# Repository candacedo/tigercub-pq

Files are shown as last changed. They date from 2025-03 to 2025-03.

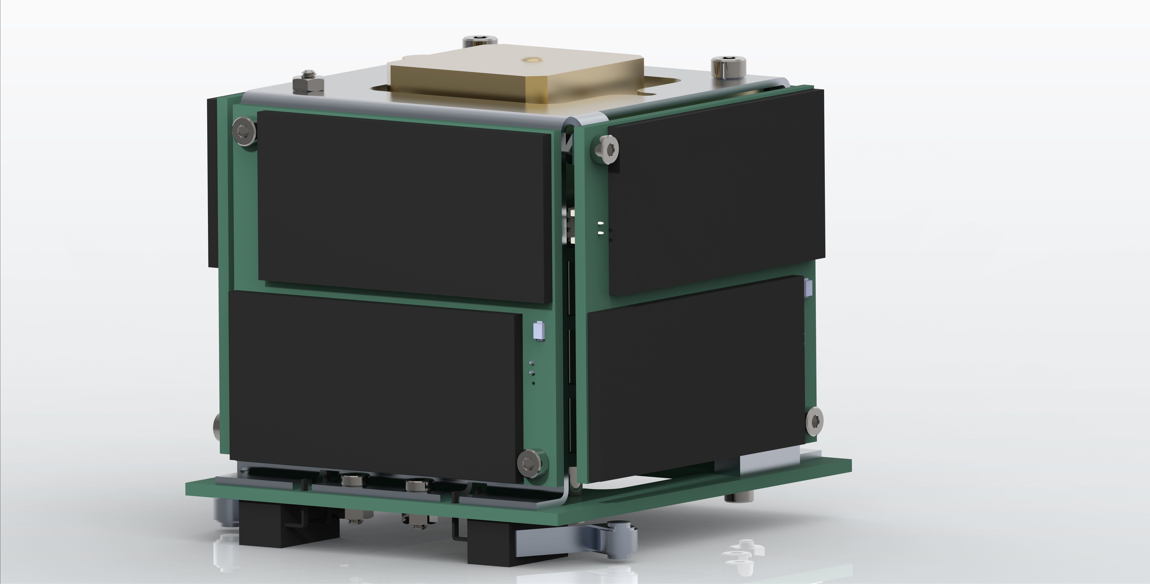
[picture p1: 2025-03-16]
CAD/full-assembly-the-beast.jpg

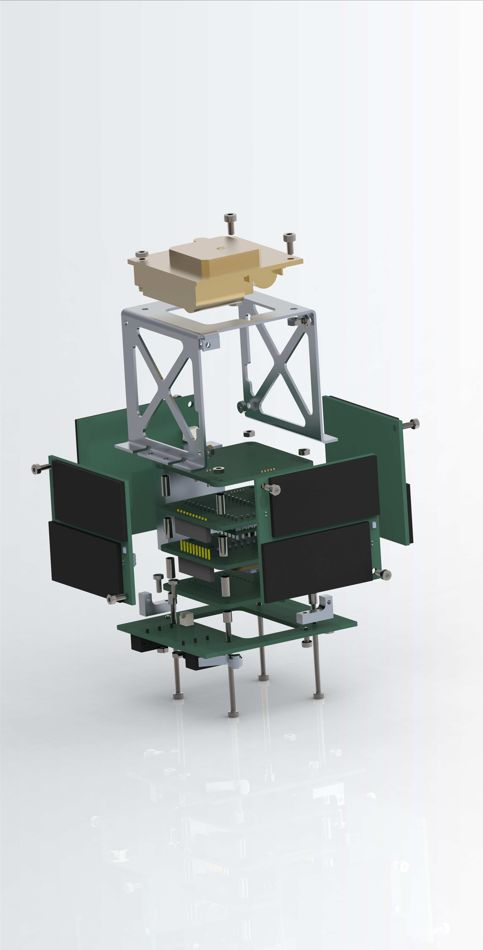
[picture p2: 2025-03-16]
CAD/full-assembly-exploded.jpg

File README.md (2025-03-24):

# TigerCub PocketQube Platform
TigerCub, an accessible, mission-agnostic PocketQube platform.

TigerCub is a satellite bus in the PocketQube form factor, designed to be accessible to students and amateur nanosatellite developers. It uses primarily commercial-off-the-shelf (COTS) components and relatively simple custom-designed PCBs, lowering barriers of entry for developers who are venturing into the PocketQube world. 

I developed TigerCub for my undergraduate senior independent work. The vast majority of design work is complete and some subsystems have been tested in laboratory environments, but the satellite bus has yet to undergo full functional testing and testing in flight-like environments. Please use at your own risk.     

## Technical Overview
TigerCub includes the following subsystems:
* on-board computer and attitude determination system,
* electrical power system,
* radio communication system, and 
* chassis.

The on-board computer/attitude determination system features an Arduino-programmable Teensy 4.0 as well as a COTS IMU and COTS MicroSD storage from SparkFun. The communication system uses the RockBLOCK 9603, a compact and lightweight communications module that transmits and receives via the Iridium network. The electrical power system is composed of a power management and distribution module designed by BHDynamics, custom-designed solar panels, and a Lithium-ion battery. These subsystems are all integrated into a sheet-metal chassis, with additional space for a payload. 

All CAD was created in PTC Creo Parametric (Version 9.0.0.0), which is free for students. All schematics and PCB designs were created in KiCAD, a free EDA software. 

## Documentation
For additional technical and operational details, including design decisions, bill of materials, power and thermal analyses, and sample code, see the "TigerCub_Report" PDF file in the repository. Please reach out to cdo32 \[at\] gatech \[dot\] edu or mgalvin \[at\] princeton \[dot\] edu for further questions. 

## Future Work & Things to Fix
A few features that should to be fixed/added (not an exhaustive list):
* Kill switches should serve as a break point between the battery and the on-board computer instead of just being connected to the on-board computer. This will involve some redesign of the backplate and wire routing. 
* Flight software needs to be developed for the EPS module and expanded upon for the flight computer. (See technical report for additional details.)
* The RockBLOCK radio system has two electrolyic supercapacitors that are a potential outgassing risk. These should be swapped out for space-qualified capacitors.
* The thermal analysis (see technical report) suggests that the spacecraft may operate outside the temperature limits of the battery. The battery should be insulated to protect it from temperature extremes. See technical report for a few suggestions.

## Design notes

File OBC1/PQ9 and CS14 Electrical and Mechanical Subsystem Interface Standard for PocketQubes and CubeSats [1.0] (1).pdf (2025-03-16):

### PQ9 & CS14 Interface Definition

Document:
Issue:
Page:

DPQ-TUD-IC-02

CC-BY-ND
This document is written and maintained by Delft University of Technology. It can be freely distributed and (parts) may be copied for own purposes with appropriate attribution and without changing the context of the information stated.

# PQ9 & CS14 Electrical and Mechanical Subsystem Interface Standard for PocketQubes and CubeSats

Description: This document defines the use and implementation PQ9 and CS14 standard.

Revision Record

Issue | Date | Author / Editor | Reviewer | Affected Sections | Description
0.1 | 15-5-17 | J. Bouwmeester | | All | Document initiation
0.2 | 22-5-17 | J. Bouwmeester | | 0 | Electrical characteristics added
0.3 | 22-5-17 | J. Chia | | Appendix A | Compatibility appendix added
0.4 | 29-5-17 | M. Boerci | | 0, 4.7, 0 | Added mechanical characteristics, reset line description and pin definition
0.5 | 17-10-17 | S. Radu | | 1,3,4 | Added scope and introduction; Changed mechanical characteristics – added spacers explanation.
0.5 | 18-10-17 | S. Radu | | 5, appendix B | Added reference data bus architecture Added appendix with drivers
0.6 | 22-11-2017 | J. Bouwmeester | | all | Rewritten towards public standard
0.7 | 23-05-2018 | J. Bouwmeester | | 5 | Modifications on data link protocol
1.0 | 04-07-2017 | J. Bouwmeester | | 4,5 | Added missing parts on grounding, termination and updated data link protocol. Document made ready for first public release.

CC-BY-ND

## Table of Contents

CC-BY-ND

## 1 Background

At Delft University of Technology (TU Delft), long term research in CubeSat electrical interface standards revealed many issues with the versatile adaptation of the PC/104 electrical interface standard. The main issuesidentified are the major amount of bus lockups on the I²C data bus interface, the volume consumption of the relatively big 104 pin connector and the potential compatibility issues arising from different manufacturers assigning different functions to unused/general purpose pins[1]. Also for power distribution the existing standards provide limited clarity and power efficiency [2]. Similar to the PC/104 implementation on CubeSats, a versatile electrical and mechanical interfaces standard under the name PQ60 already exists [3].

The versatility of the PC/104 and PQ60 standards, having multiple data busses to choose from and the freedom to allocate custom signals or power to general purpose pins, are appreciated by many engineers. Since both standards are implemented already in commercial products at the time of initiation of this document, they are a logical option to consider as main bus standard. However, the definition of a lean and unambiguous alternative standard for PocketQubes and CubeSats was deemed necessary in attempt to overcome identified issues and be prepared for the future.

The aim in selecting the interface standard for the satellites developed at TU Delft was to have lean, small, efficient and resilient interface. For selecting the data bus, I²C, Differential I²C, CAN and RS-485 were taking into consideration and the main criteria were robustness, power consumption, effective data throughput and legacy support were taken into account. The details of the trade-off can be found in a journal paper [4]. The PocketQube and CubeSat community has been involved in the research and the trade-off process for the data bus with the aid of surveys. However, the detailed definition of the PQ9 and CS14 standards are performed at TU Delft to aid a rapid definition process and avoid compromising its lean philosophy.

## 2 Use of the Standard

The standard is open, non-proprietary and free to use for commercial and non-commercial entities. The PQ9 and CS14 standards are not trademarked. However, the logos may only be used for systems which are fully compliant to the respective standards. New (derived) standards should use a different logo and naming in order to avoid confusion and to maintain the lean philosophy and unambiguous implementation of PQ9 and CS14.

Delft University of Technology will remain the responsible entity for the maintenance of this document. In the near future, potential updates will focus on the clarity, correctness and completeness of the document. Comments from the community related to the documents and the specified details are welcome. Changes to the standard on the high level are undesired and will not occur if no major flaws will be discovered during the verification process which is expected early 2018. Future improvements of the standard will only be performed when the interface becomes a limiting factor for the state-of-the-art technology. This is not expected in upcoming years and when this is deemed necessary the aim will be to provide backwards compatibility with the existing standard.

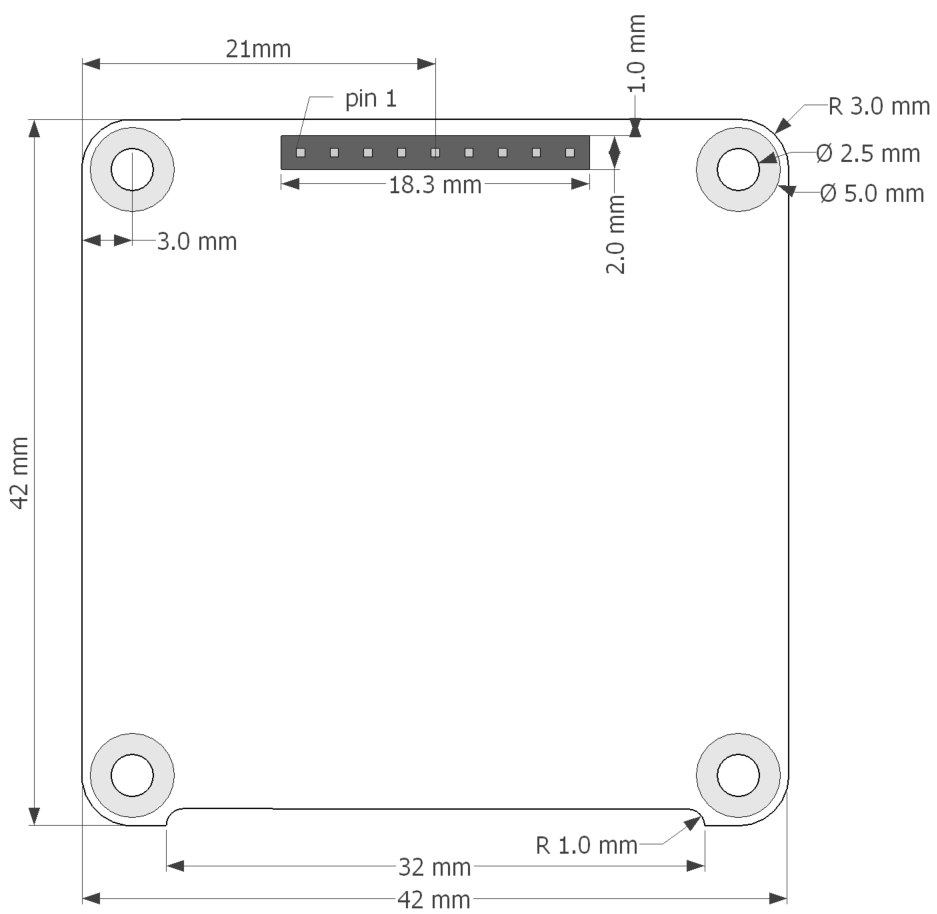
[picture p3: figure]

CC-BY-ND

## 3 Mechanical Characteristics

Each physical subsystem will be placed in a stack and has standard outer (PCB) dimensions and four holes for mechanical fixation to the rest of the systems and/or satellite body. The mechanical outline of the boards are compatible to the CubeSat Design Specification [5] and the PocketQube Standard [6].

### 3.1 In-Plane System Envelope

The standard Printed Circuit Board (PCB) outline of PQ9 and CS14 is provided in Figure 1 and Figure 2 respectively. The room between the edges of the PCB and the outer structure of the satellite can be used by cabling and extensions toward the outside of the satellite. It is recommended to limit in-plane extensions of components and use of flexible wiring which can be rerouted when necessary.

Figure 1. PQ9 printed circuit board outline

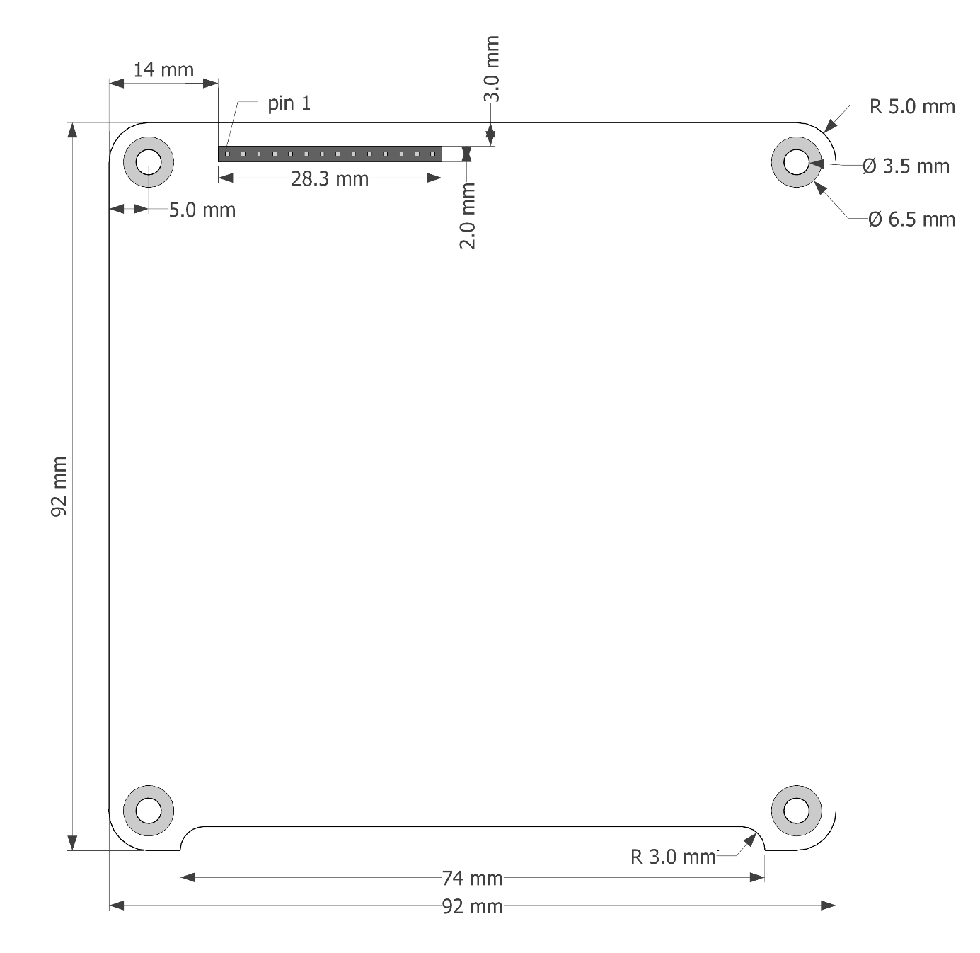
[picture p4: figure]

CC-BY-ND

Figure 2. CS14 printed circuit board outline

### 3.2 Out-of-Plane System Envelope

The out of plane dimensional constraint depends on the selection of the connector(s) and possible configurations. The following requirements have to be taken into account:

- Each system has a minimum (out-of-plane) component height of 2 mm on the bottom side of the PCB. This minimum value is used for a system with only leads on the bottom of a small connector. Note that the connector of the system below protrudes into the system envelope under consideration.
- A 1 mm margin is required between components on the top side of the PCB and possible components on the bottom side of the next PCB.
- The PCB thickness is assumed to be 1.6mm. In case of other PCB thickness, the potential configuration(s) need to be recalculated. Please pay attention to the minimum and maximum pin insertion depth.

CC-BY-ND

- The maximum pin soldering height is 0.65 mm.
- The rods or threaded stand-offs thread diameter is M2 for PocketQubes and M3 for CubeSats.
- The outer diameter of the spacers or stand-offs is 5 mm for PocketQubes and 7 mm for CubeSats.

The reference connector is the Samtec SQT-1xx-xx-LS series, which provides the input stated below.

- The connector height is equal to 6.35 mm [RD01]
- The pin (lead) length of the small connector (SQT-109-03-LS for PocketQubes, SQT-114-03-LS for CubeSats) is equal to 5.28 mm [RD01]
- The pin (lead) length of the large connector (SQT-109-02-LS for PocketQubes, SQT-114-02-LS for CubeSats) is equal to 15.24 mm [RD01]
- The insertion depth is required to be between 2.62 and 5.03 mm [RD01], whereas for PQ9 and CS14 the minimum and maximum considered insertion depths are respectively 3 and 5 mm.
- Connectors if different vendors may be considered is they are fully compatible with the reference connector. In case the potential pin (lead) lengths are different, the potential configurations need to be recalculated.

CC-BY-ND

Figure 3 and Table 1 provides an example based on two systems using the small connector and a board to board distance (spacer) of 7 mm in between.

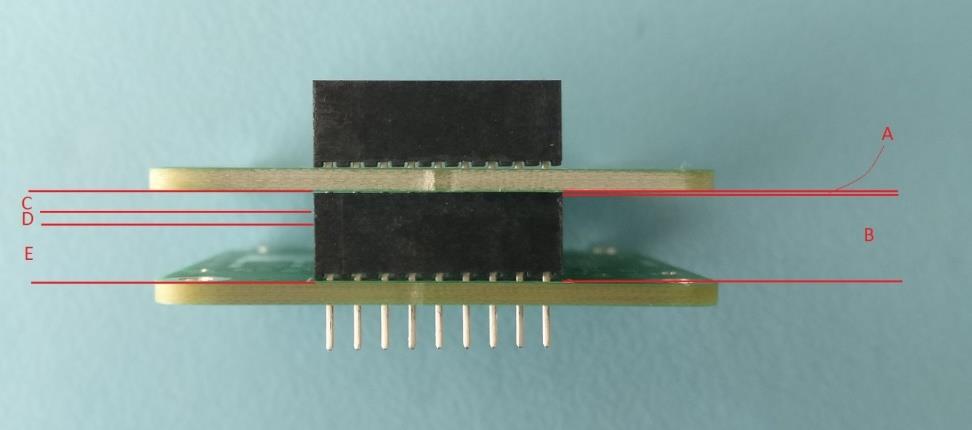
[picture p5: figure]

Figure 3: Out-of-plane constraints example (option I)

Table 1: Values of maximum component height and insertion depth (option I)

Symbol | Description | Value [mm]
A | Maximum soldering pad height | 0.65
B | Connector height | 6.35
C | Maximum height of components placed underneath upper PCB | 2.00
D | Margin between components of two adjacent PCBs | 1.00
E | Maximum component height | 4.00
tPCB | PCB thickness | 1.60
Lpins,small | Pin length of the small connector | 5.28
Idepth | Pin Insertion Depth | 3.03

CC-BY-ND

Table 2 provides the values for different configurations of the small and large reference connector. When using these values, please check if they comply with the assumptions made.

Table 2: Configuration possibilities with small and large connectors

Description | Max. comp. height above PCB [mm] | Max. comp. height below PCB [mm] | Board spacing dist.¹ [mm] | Pin insert depth [mm] | Stack height inc. 1mm margin [mm] | Example Image

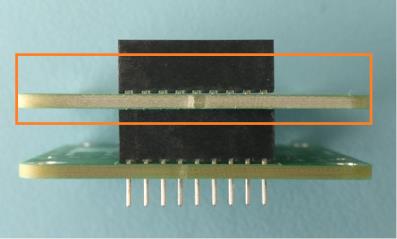
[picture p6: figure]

Option I: single small connector on top | 4.0 | 2.0 | 7.0 | 3.0 | 8.6 mm

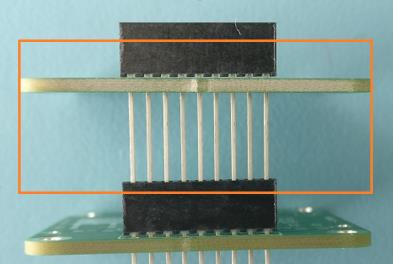
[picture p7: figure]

Option II: single large connector on top | 4.0 4.0 4.0 | 10.0 11.0 12.0 | 15.0 16.0 17.0 | 5.0 4.0 3.0 | 16.6 17.6 18.6

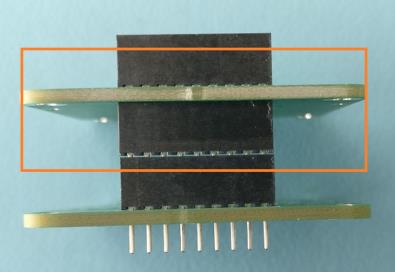
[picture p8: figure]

Option III: small connector on top, small connector glued on bottom² | 4.0 | 9.0 | 14.0 | 3.9 - 4.6 | 15.6
Option IV: double small connector stacked on top³ | 11.0 | 2.0 | 14.0 | 3.0 | 15.6

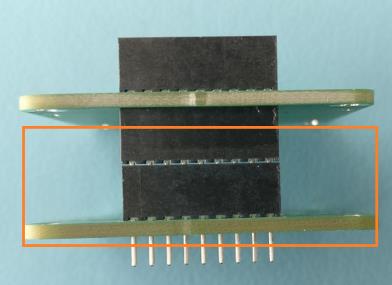
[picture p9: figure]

1) This board spacing distance stated is the distance from the PCB surface of the largest side to the next system’s PCB surface, assuming that the next system uses only a single small connector. In case the next system uses a different configuration, spacing distance needs to be calculated for this configuration.
2) fixation of bottom connector (e.g. with glue) at a spacing distance between 0.0 and 0.65 mm from the PCB is essential to prevent that this connector can slide downwards and the connector on top goes below minimum insertion depth.
3) Fixation of stacked connector at exactly 0.65mm spacing (e.g. with glue) is required to prevent that the insertion depth of the PCB above goes below minimum insertion depth.

CC-BY-ND

table continued

Description | Max. comp. height above PCB [mm] | Max. comp. height below PCB [mm] | Board spacing dist.¹ [mm] | Pin insert depth [mm] | Total stack height inc. 1mm margin [mm] | Example Image

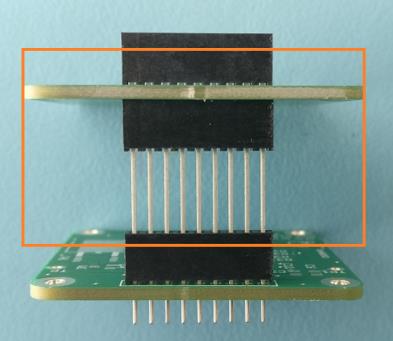
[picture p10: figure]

Option V: small connector on top, large connector on bottom | 4.0 | 19.0 | 24.0 | 3.9 - 4.6 | 25.6

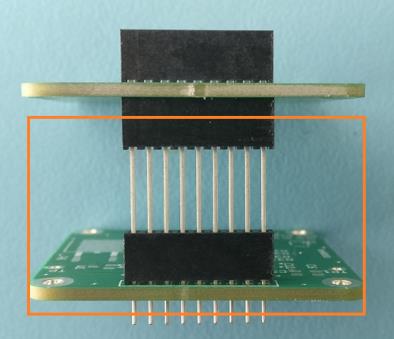
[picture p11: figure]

Option VI: small connector on top, large connector stacked on top of small connector | 21.0 | 2.0 | 24.0 | 3.9 -3.6 | 25.6
Option VII: large connector on top, large connector on bottom | 4.0 4.0 | 27.0 28.0 | 32.0 33.0 | 4.6 – 5.0 3.6 – 5.0 | 33.6 34.6

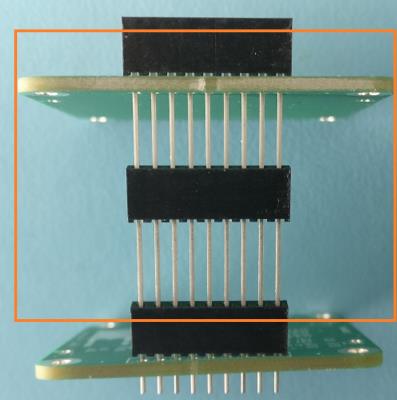
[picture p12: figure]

1) This board spacing distance stated is the distance from the PCB surface of the largest side to the next system’s PCB surface, assuming that the next system uses only a single small connector. In case the next system uses a larger sizing as well, spacing distance needs to be calculated for this configuration.

CC-BY-ND

## 4 Electrical Characteristics

### 4.1 Pin Definition

Both PQ9 and CS14 are based on a single linear RS-485 data bus, several unregulated power distribution lines, a few (common) ground lines and a reset line.

The PQ-9 and CS14 interface connector pin allocations are represented in Figure 4 and Figure 5 respectively and their definition is stated in Table 3.

Figure 4. PQ9 (pin 1-9) interface connector

Figure 5. CS14 interface connector

Table 3. Pin allocation for PQ9/CS14 standard interface

Pin | Signal | Allocation
1 | RST | system reset line (60 Ω to gnd)
2 | 485-B | RS-485 inverting signal
3 | 485-A | RS-485 non-inverting signal
4 | GND | Ground
5 | V1 | rec.: OBC (PQ: + Radio)
6 | V2 | rec.: ADCS (PQ: + GNC)
7 | V3 | rec.: propulsion
8 | V4 | rec.: primary payload(s)
9 | GND | Ground
10 | V5 | rec.: radio
11 | V6 | rec.: GNC
12 | V7 | rec.: data storage & payload
| | data transmitter
13 | V8 | rec.: secondary payload(s)
14 | GND | ground

### 4.2 RS-485 Clock Frequency

The internal microcontroller’s UART will be set at a baud rate of:

500 kbit/s (500,000 bit/s) for PQ9

and

1 Mbit/s (1,000,000 bit/s) for CS14.

The clock at any subsystem may not be off by more than +/- 0.5% to ensure reliable communications. It is recommended to select the general clock frequency of the microcontroller at least 16 times higher than the baud rate (this yields 8 MHz for PQ9 and 16 MHz for CS14) .

1

RST

2

485A

3

485B

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
485A

3

485B

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
CC-BY-ND

### 4.3 RS-485 Compatible Microcontrollers

The microcontroller should have a UART which supports the stated clock frequency. The UART should also support 9 bits between start and stop conditions (see byte definition in section 5.1). However, it is recommend that a hardware controlled address bit detection which triggers and interrupt is included to limit the amount of data (interrupts) which need to be processed by the microcontroller. Developers using the standard should always check if a chosen microcontroller supports the byte and packet definition. Appendix A shows the compliance of a selection of microcontrollers with these requirements.

### 4.4 RS-485 Differential Drivers

There is a wide variety of differential drivers which can be chosen. In the current version of the standard no specific recommendations are given. An important criteria is the supported baud rates. For PQ9 this should be at least 500 kbit/s, for CS14 it should be 1 Mbit/s. Furthermore, the size of the integrated circuit and its power consumption could be important criteria to consider for which significant differences between options can be expected. Finally, slew rate limited devices are more immune to noise but it comes at the expense of a restricted supported data rate.

### 4.5 RS-485 Termination and Biasing

Reflection is not really a concern up to 1 MHz for PocketQubes and CubeSats, since the wavelength (~300m) in this case is orders of magnitude longer than the line length. There is thus no need to put the termination at the end of the lines to suppress reflection. For increased noise immunity however, single termination at an arbitrary point along the line is highly recommended. The chosen location for the standard is the physical board which acts as the central unit for the electrical power distribution. The reason is that such a system is always required for the CS14 and PQ9 interface standard to distribute power. A central on-board computer, being a likely master node for RS-485, is more likely to be redundant or could be integrated with another physical subsystem, yielding potential missing or redundant termination resistors in the system. The termination resistance should be 60 Ω or more. The higher the resistance, the lower the power consumption but this also reduced noise immunity.

Old generation differential drivers specify bias resistors to enforce a logic high during idle state by pulling line A to the reference voltage and line B to ground. The bias resistors can only be implemented if there is also a termination resistor and it is recommended to have a bias resistor value of 5 to 10 times the termination resistance. This forces the operation out of the undefined region between +/-200 mV. New generation RS-485 drivers, such as the LTC1480, MAX3471 and TI SN64HVD7x have an internal fail-safe feature which do not require external biasing anymore. However, for enhanced noise immunity it can still be implemented.

### 4.6 Power Distribution Voltage Level and Current Limits

The distribution voltage levels are:

PQ9: 3.0 V – 4.1 V
CS14: 6.0 V – 8.2 V

CC-BY-ND

These levels are based on a single Li-Ion battery cells and two in series respectively. By distributing unregulated battery voltage levels and leaving potentially required regulation to fixed voltage levels to the local subsystems, complexity is avoided and conversion efficiency losses are minimized [3].

The absolute maximum current is 4 A per distribution line, as determined by the connector specification assuming a maximum internal temperature of 60 °C [6]. The allowed current levels can however be lower due to the battery limitations and the power budget. It is recommended to include programmable current limiters for each distribution line.

In-rush current limits are not yet specified in this standard. Therefore, the specifications of the chosen central electrical power distribution unit needs to be followed. It is generally recommended to limit the in-rush current as much as possible at the subsystem loads.

### 4.7 Grounding Topology

The ground pins on the PQ9 and CS14 function as common reference ground as well as power return path. This could lead to small voltage difference across a stack of physical subsystems due to their power consumption. According to [2], an extreme case of stack of 10 boards over 20 cm distance w.r.t. the electrical power distribution unit, would yield 44 mΩ resistance for one grounding path. Assuming that this should carry a return current of 4A, a maximum ground voltage offset of 200 mV can be expected. To minimize ground loops, it is important that electrically conducting structural components (for example metallic stand-offs or spacers at the corners) are only connected to the ground via a resistor of at least 1 kΩ to ensure that the electrical interface ground carries the current and not the structural elements. All electronic circuits must be connected to the PQ9/CS14 ground with a minimal path resistance.

### 4.8 Reset Line

A global power reset will be triggered when the line is pulled high for at least 20 ms to a minimum threshold voltage of 2 V and at maximum 5 V. At both sides of the reset line, this period should be ensured with margins appropriate for the circuit and its (thermal) environment. The driving circuit can be placed e.g. at the radio command receiver (for a tele-commanded reset) or at the on-board computer (for automatic failure detection, isolation and recovery purposes).

After a reset has been triggered, the central EPS unit is required to switch off the distribution power to all subsystems and its own microcontroller for 2000 ms. All subsystems should ensure that local power has dropped to a level which guarantees a complete power-out of volatile memory and register states within 2000 ms taking appropriate margins into account.

CC-BY-ND

A standard filter and protection circuit shall be implemented close to the power reset (integrated) circuit:

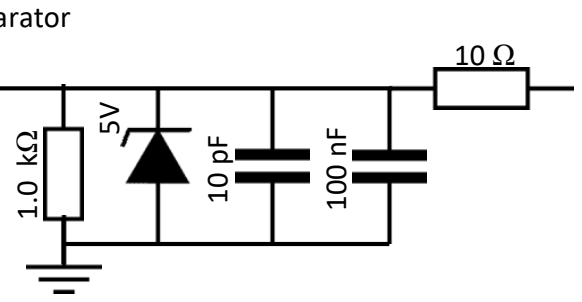
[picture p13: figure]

The shunt bias resistor pulls the line low in idle conditions. A minimum direct current of 2 mA is required to pull the line to the threshold voltage.

The input series resistors in combination with the Zener diode protects the circuit for excessive voltage levels due to electrostatic discharge and particle radiation.

The RC filter caps have a cut-off frequency of 1.6 kHz and 16 MHz to filter out power transient and RF noise respectively.

PQ9 connector

comparator
input

CC-BY-ND

## 5 Data Link Protocol

The data protocol used for PQ9 is currently only defined at the data link layer.

### 5.1 Byte Definition

- The chronological order is Least Significant data Bit (LSB) first
- Each byte begins and ends with a start and stop bit (UART standard)
- The address interrupt bit follows after the Most Significant data Bit (MSB). When this bit is 1, the byte contains an destination address. For any other type of byte it is 0.

This figure relates to the chronological order and not the logical order where bit 7 is on the left.. Please note that for human interpretation the 8 content bits need to be reversed in order (bit 7 on the left).

### 5.2 Packet Definition

- Destination/Source Address:
- Defines the source and destination of the packet.
- Supports up to 254 nodes (inc. master).
- Master address: 0x00.
- General call address: 0xFF.
- Slave address: anything between 0x01 and 0xFE.
- Message Size:
- Defines the length of the message in bytes.
- Size=0x00 is used for acknowledgements.
- Supports messages up to 255 bytes.
- Refers only to the message content, so total packet size is message size + 5 bytes.
- CRC:
- CRC-16 CCIT
- Initialized on seed: 0xFFFF
- Calculated on complete packet (so address, size + message data)
- Calculated on least significant bit first
start | 0 | 1 | 2 | 3 | 4 | 5 | 6 | 7 | address | stop

destination
adress
[8 bit]

message
size
[8 bit]

source
address
[8 bit]

message
[0-255 bytes]

CRC
[16 bit]

CC-BY-ND

### 5.3 Data Transactions

There is only a single master node active at a time. All other devices are slave nodes and only respond upon request of the master. A redundant/back-up node which is slave or off in nominal conditions can take over the master functionality provided that the nominal master is not active on the bus anymore.

There are three types of transactions:

### 1. Individual message

master → slave

slave → master

### 2. Data request

master → slave

slave → master

### 3. General call

master → slave

slaves do not respond (this should be enforced at each slave when called on the general address)

slave
address

message
size

master
0x00

one-way command/data

CRC
[16 bit]

master
0x00

ack.
0x00

slave
address

CRC
[16 bit]

slave
address

message
size

master
0x00

data request command

CRC
[16 bit]

master
0x00

ack.
0x00

slave
address | response data

CRC
[16 bit]

all
0xFF

message
size

master
0x00

one-way command/data

CRC
[16 bit]

CC-BY-ND

### 5.4 Error Handling

CRC Failure

When the CRC failed, the data packet should be discarded as a whole by the microcontroller. This minimizes the chance that slaves respond on a message which was not meant for them (e.g. bitflip on destination address) or master or slave start to interpret noise.

Time-out

The maximum time-out is 100 ms, including latency and time intervals between bytes. The counter starts at the master after the destination address byte is sent and by the slave when the it identifies its own address (or the general address). When the entire transaction is not completed within this time, both slave and master discard the information which is send. The master will internally flag that the transaction is timed-out, such that it could potentially be used by the application layer for error handling.

## 6 References

1. Bouwmeester J. et al., Survey on the implementation and reliability of CubeSat electrical bus interfaces, CEAS Space Journal Vol 9, . doi: 10.1007/s12567-016-0138-0, 2017.
2. Bouwmeester J. and Santos N., Analysis of the Distribution of the Electrical Power in CubeSats, The 4S symposium. ESA, Valetta, 2014.
3. Becnel E. et al., PQ 60 Standard Document (v1.1), 2015.
4. Bouwmeester J. et al., Towards an innovative electrical interface standard for PocketQubes and CubeSats,. Adv Sp Res. doi: 10.1016/j.asr.2018.03.040, 2018.
5. California Polytechnic State University., Cubesat design specification, 2009.
6. Radu S. et al., The PocketQube Standard, 2018.

CC-BY-ND

## Appendix A Microcontroller-Byte Definition Compatibility

A sample selection is made of 8 microcontrollers (to be) used in PocketQubes and CubeSats, to check if the UART controller supports the byte definition, with emphasis on the address bit as interrupt. The results are provided in the following table:

Manufacturer | Microcontroller | Satellite | Can an address bit (9-bit UART) be implemented on the micro-controller? | Does the address bit trigger a dedicated interrupt? | Note
Texas Instruments | MSP432 | Delfi-PQ | Y | Y | MSP432 Technical Reference manual, pg 725-753 Keyword: Address-Bit Multiprocessor Format, pg 729
Texas Instruments | MSP430 | Alba Orbital OBC | Y | Y | MSP430 User's Guide, pg 571- 599 Keyword: Address-Bit Multiprocessor Format, pg 575
Atmel | AT91SAM9G20 | ISISpace CubeSat OBC | Y | Y | Atmel SAM9G20 datasheet pg 354-376, 481-535 Keyword: Multidrop mode, PARE, pg 500
ARM | Cortex-M3 STM32F103C8T6 | AAUSAT-3, OzQube camera module | ? | Y | RM0008 Reference manual, pg 790-832 Keyword: Address mark detection, WAKE, RXNE flag, pg 806 Address bit at MSB, used 4-bit address format, the 4-bit address is at LSB
Atmel | AT32UC3C | GOMSpace CubeSat OBC | Y | Y | Atmel AT32UC3C datasheet pg 562-656 Keyword: Multidrop mode, PARE, pg 584
Atmel | ATmega328P | Arduino, OzQube, ArduiQube | Y | Y | Atmel ATmega328/P datasheet pg 225-253 Keyword: Multi-Processor Communication Mode, pg 239
ARM | Cortex-M4 MK20DX256 | Ubo PocketQube, Smog-1 | Y | Y | K20 Sub-Family Reference Manual pg 1201-1296 Keyword: Match address operation, pg 1274
MicroChip | PIC32MM0064FP L028 | Low power, latest generation | Y | Y | PIC32MX Family Reference Manual pg 699-752 Keyword: Address Detect Mode, pg732

### PQ9 & CS14 Interface Definition

Issue:
Page:

1.0
18 / 19

CC-BY-ND
This document is written and maintained by Delft University of Technology. It can be freely

## Appendix B Potential RS485 drivers

The list below provide a list of potential RS-485 drivers which can be used with their key specifications. Note that this list is not complete and will not be kept up to date. It focusses on the data rates required for PQ9 and CS14 and is limited to solder mounted devices.

No | | | Max. Data rate (Mbit /s) | Curr ent (idle, Rx on) [mA] | Power (driving, 120Ω termin ation) [mA] | Packa ge | width (mm) | lengt h (mm) | Voltage range | Temp. Range (deg C) | Featu res | Datasheet
1. | Intersil | ISL32455 EIUZ | 1 | 2.1 | 54 or 100 | 8-MSO P | 3.05 | 5.05 | 3 | 5.5 | -40 | 85 | +-60V Fault | https://www.intersil.com/content/dam/Intersil/documents/isl3/isl32450e-52e-53e-55e-57e.pdf
2. | Intersil | ISL32455 EIBZ | 1 | 2.1 | 54 or 100 | 8-SOIC | 3.05 | 5.05 | 3 | 5.5 | -40 | 85 | +-60V Fault | https://www.intersil.com/content/dam/Intersil/documents/isl3/isl32450e-52e-53e-55e-57e.pdf
3. | Intersil | ISL32435 EIUZ | 1 | 2.1 | 54 or 100 | 8-MSO P | 3.05 | 5.05 | 3 | 5.5 | -40 | 85 | +-40V Fault | https://www.intersil.com/content/dam/Intersil/documents/isl3/isl32450e-52e-53e-55e-57e.pdf
4. | Intersil | ISL32435 EIBZ | 1 | 2.1 | 54 or 100 | 8-SOIC | 3.05 | 5.05 | 3 | 5.5 | -40 | 85 | +-40V Fault | https://www.intersil.com/content/dam/Intersil/documents/isl3/isl32430e-32e-33e-35e-37e.pdf
5. Exar | Corporati on | XR33155 | 1 | 4 | 120 | 8-SOIC | 3.05 | 5.05 | 3 | 5.5 | -40 | 85 | +-60V Fault | https://www.intersil.com/content/dam/Intersil/documents/isl3/isl32430e-32e-33e-35e-37e.pdf
6. Exar | Corporati on | XR33038 | 1 | 0.3 | 120 | 8-NSOI C | 6 | 5 | 2. 8 | 5.5 | -40 | 85 | +-18V Fault, receiv er input filteri ng | https://www.exar.com/ds/xr33152-xr33155-xr33156-xr33158.pdf

### PQ9 & CS14 Interface Definition

Issue:
Page:

1.0
19 / 19

CC-BY-ND
This document is written and maintained by Delft University of Technology. It can be freely
7. Exar | Corporati on | XR33035 | 10 | 0.3 | 120 | 8-NSOI C | 6 | 5 | 2. 8 | 5.5 | -40 | 85 | +-18V Fault, receiv er input filteri ng | https://www.exar.com/ds/xr33032-35-38_v100_022814.pdf
8. Maxim | Integrate d | MAX147 82EAUA | 1 | 1.9 | 54 or 100 | 8-SO | 5 | 6.2 | 3 | 5.5 | -40 | 85 | | https://www.exar.com/ds/xr33032-35-38_v100_022814.pdf
9. Maxim | Integrate d | MAX147 82EATA | 0.5 | 1.9 | 54 or 100 | 8-TDFN -EP | 3.1 | 3.1 | 3 | 5.5 | -40 | 12 5 | | http://datasheets.maximintegrated.com/en/ds/M AX14782E.pdf
10. Maxim | Integrate d | MAX147 82EASA | 0.5 | 1.9 | 54 or 100 | 8-uMA X | 3.1 | 5.03 | 3 | 5.5 | -40 | 12 5 | | http://datasheets.maximintegrated.com/en/ds/M AX14782E.pdf
11. Maxim | Integrate d | MAX134 30EETB | 0.5 | 1 or 2 | 54 or 100 | 10-TDFN -EP | 3.1 | 3.1 | 3 | 5 | -40 | 12 5 | slew rate limite d | http://datasheets.maximintegrated.com/en/ds/M AX14782E.pdf
12. Maxim | Integrate d | MAX134 30EEUB | 0.5 | 1 or 2 | 54 or 100 | 10-uMA X | 3.1 | 3.1 | 3 | 5 | -40 | 85 | slew rate limite d | http://datasheets.maximintegrated.com/en/ds/M AX13430E-MAX13433E.pdf
13. Holt | Integrate d Circuits | HI4850 | 0.5 | 10 | 54 min | 8-SOIC | 3.05 | 5.05 | 3 | 5.5 | -55 | 12 5 | | http://datasheets.maximintegrated.com/en/ds/M AX13430E-MAX13433E.pdf

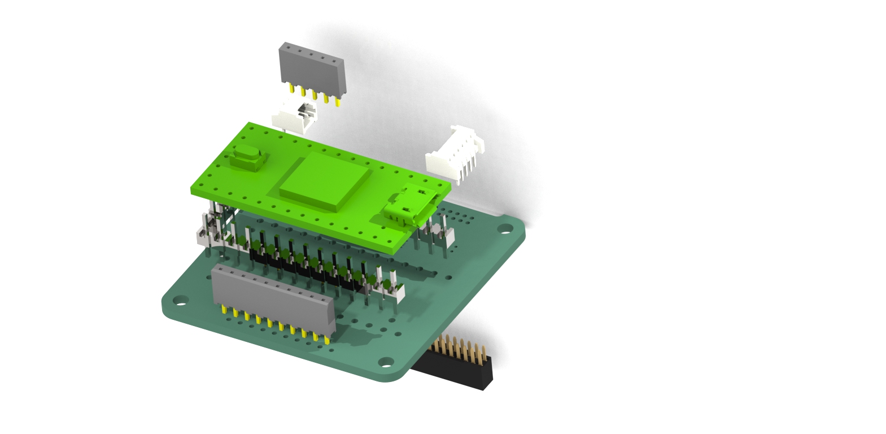
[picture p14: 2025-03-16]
CAD/obc1.jpg

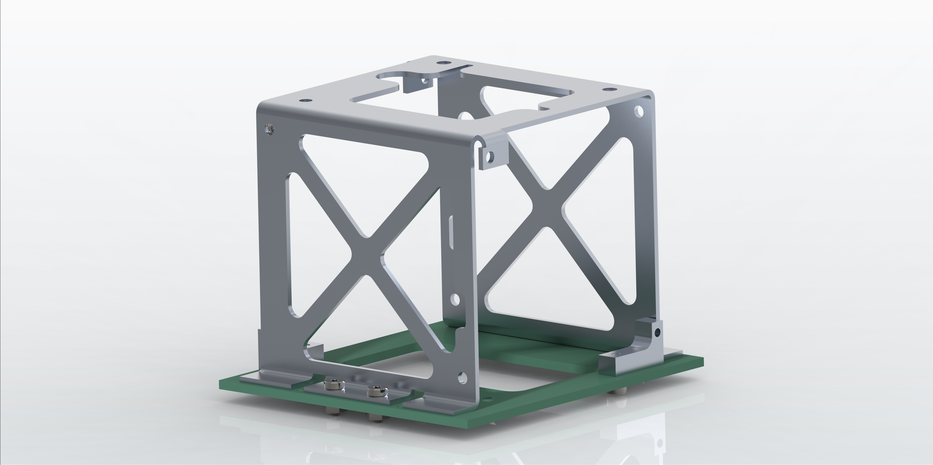
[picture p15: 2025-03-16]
CAD/structure-render.jpg

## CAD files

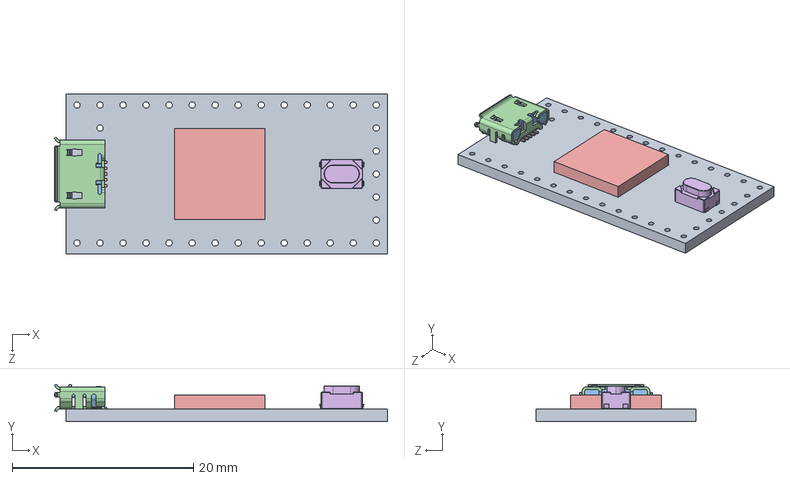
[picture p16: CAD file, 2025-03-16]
CAD/Teensy_4.0_Assembly.STEP
36.8 x 4.12 x 17.7 mm
Teensy_4.0_PCB
Micro USB-B Female 5Pin SMD
NXP iMXRT1062
SKRPACE010 v4

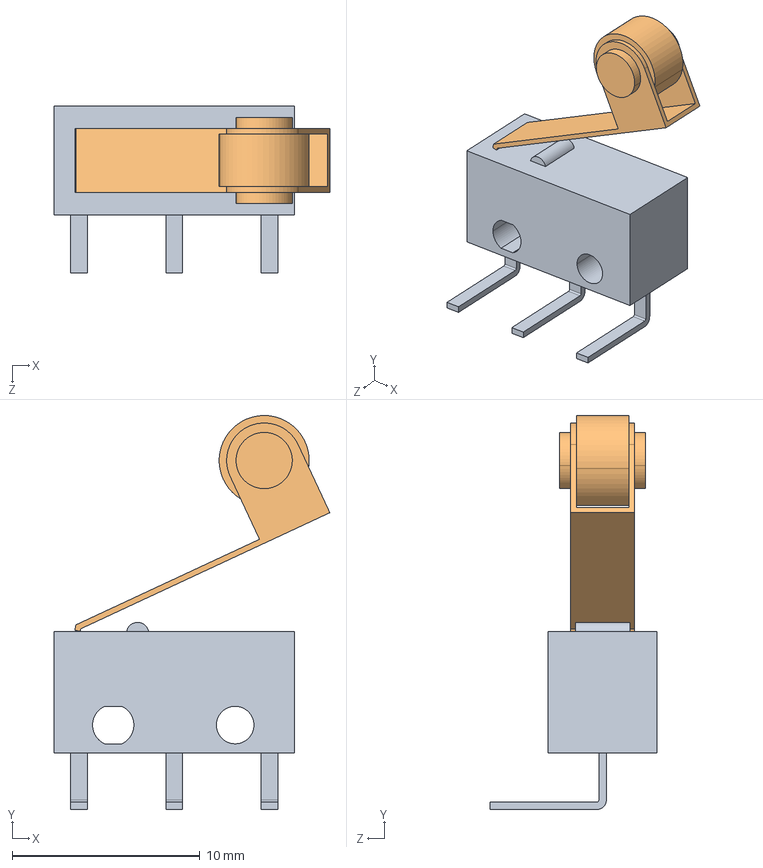
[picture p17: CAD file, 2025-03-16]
Backplate/D2F_L2_A1.step
14.7 x 21.0 x 8.90 mm
D2F_L2_A1_BASE
D2F_L2_A1_ACTUATOR

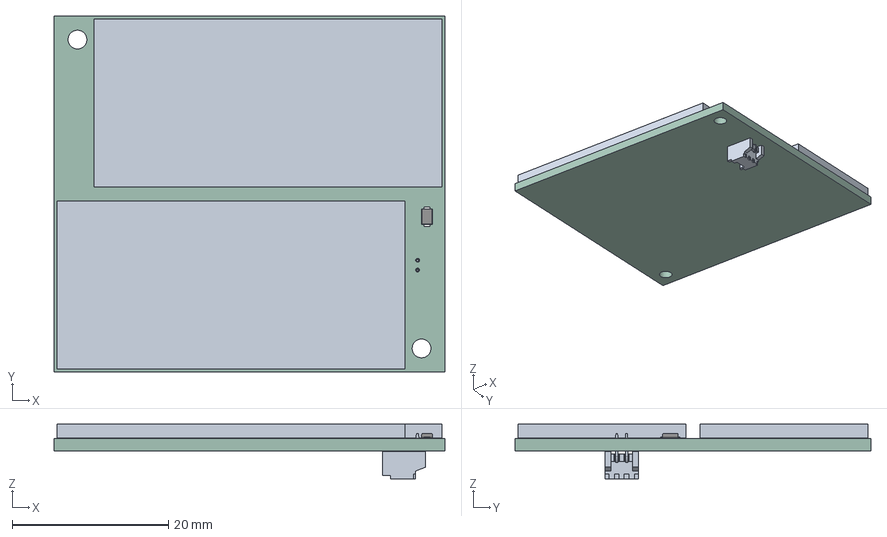
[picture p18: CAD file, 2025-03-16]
Solar Panels/PV1/pv1.step
50.0 x 45.5 x 7.00 mm
SM940K09L x 2
CUHS20S30,H3F
pv1 PCB

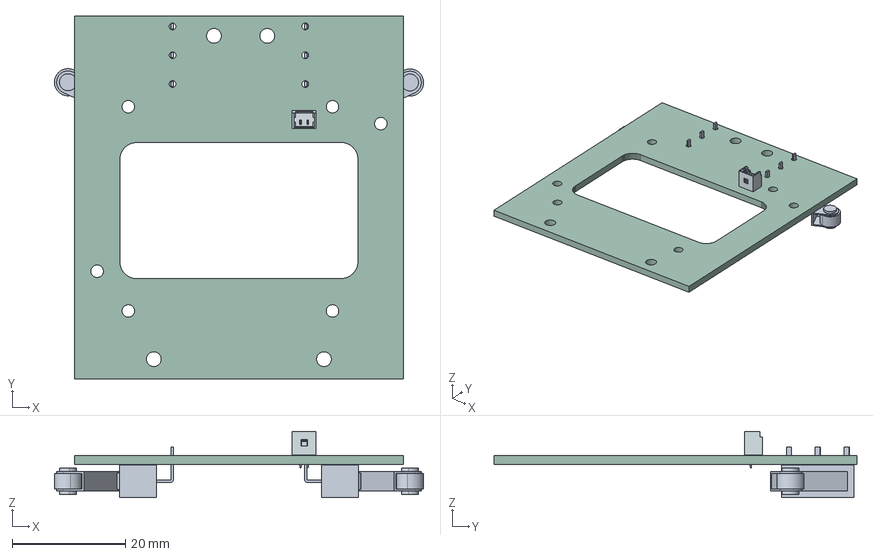
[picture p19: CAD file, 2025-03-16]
Backplate/kill-switch-board.step
65.1 x 64.0 x 11.7 mm
D2F_L2_A
D2F_L2_A1
530470210wbm000_01
kill-switch PCB

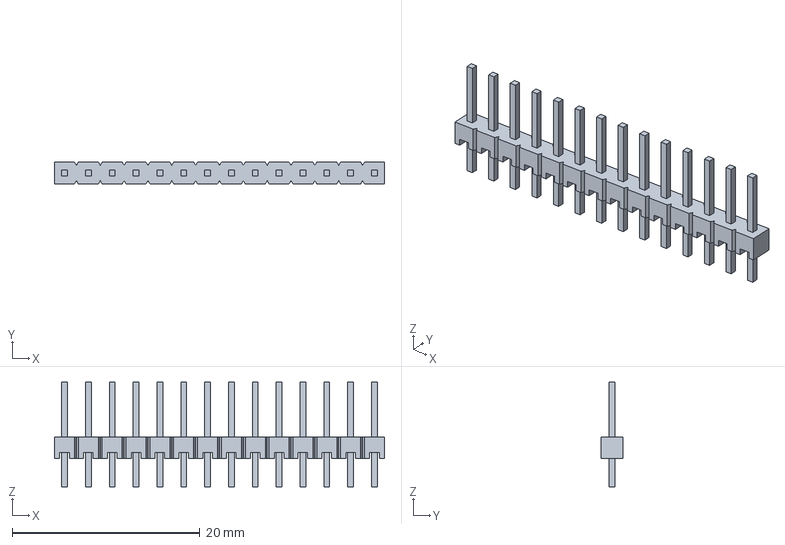
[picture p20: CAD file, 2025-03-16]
CAD/1-146282-4.step
35.2 x 2.34 x 11.2 mm

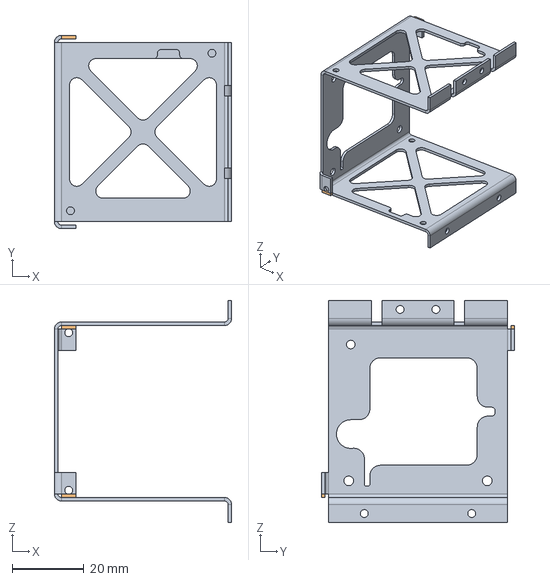
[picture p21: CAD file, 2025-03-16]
CAD/pq-walls-4-19.stp
49.5 x 54.0 x 62.0 mm

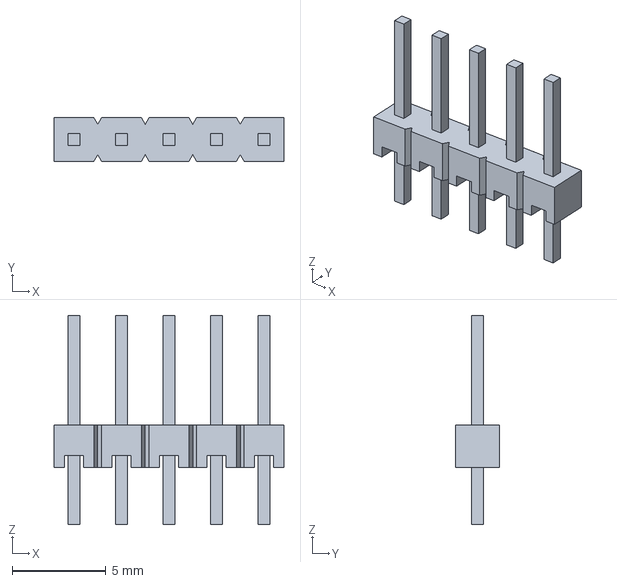
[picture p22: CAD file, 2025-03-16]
CAD/5-146282-5.step
12.3 x 2.34 x 11.2 mm

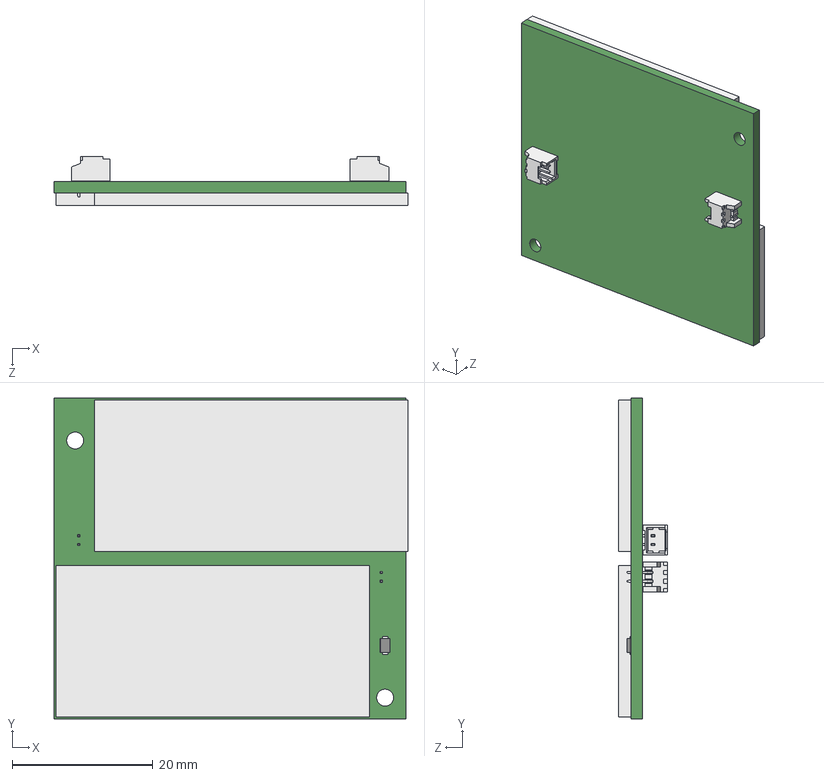
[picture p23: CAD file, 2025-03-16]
CAD/PV_Panel_Near_LowerHole.step
50.2 x 45.5 x 6.99 mm
Board_PV_Panel_Near_LowerHole
CUHS20S40,H3F
pq-solar-panel x 2

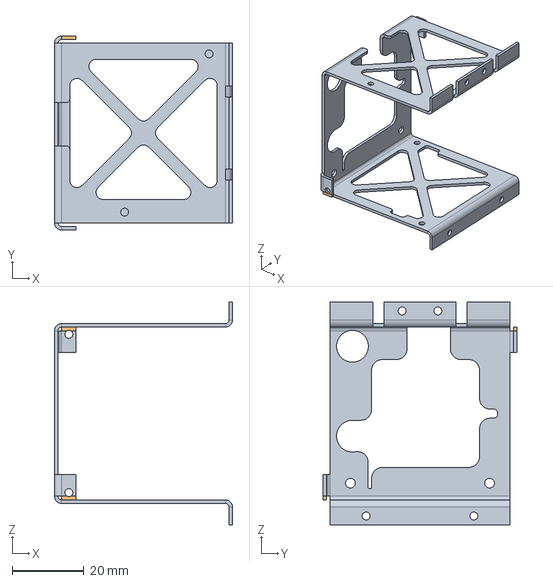
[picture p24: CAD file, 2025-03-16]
CAD/pq-walls.stp
49.5 x 54.0 x 62.0 mm

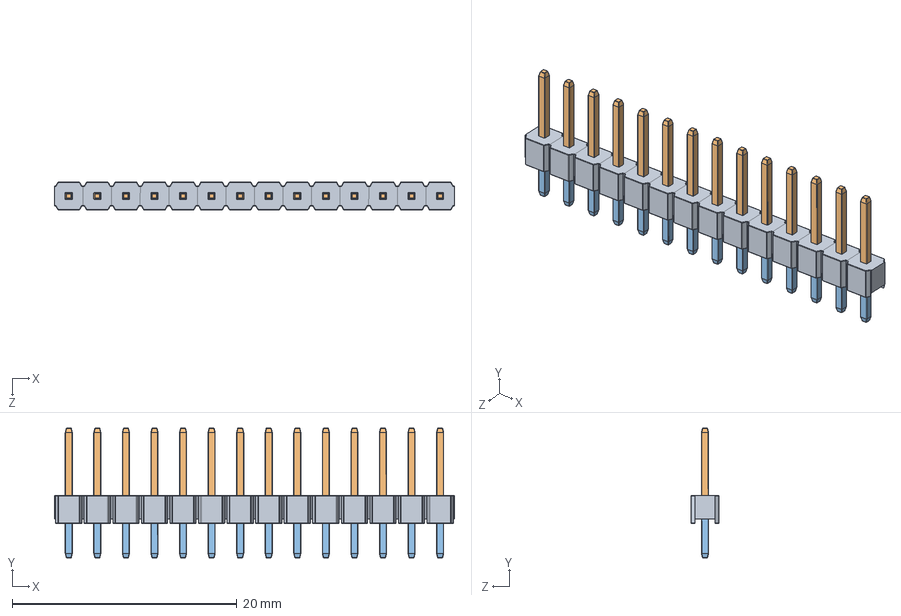
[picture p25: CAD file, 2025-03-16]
CAD/PH1-14-UA.STEP
35.6 x 11.6 x 2.50 mm

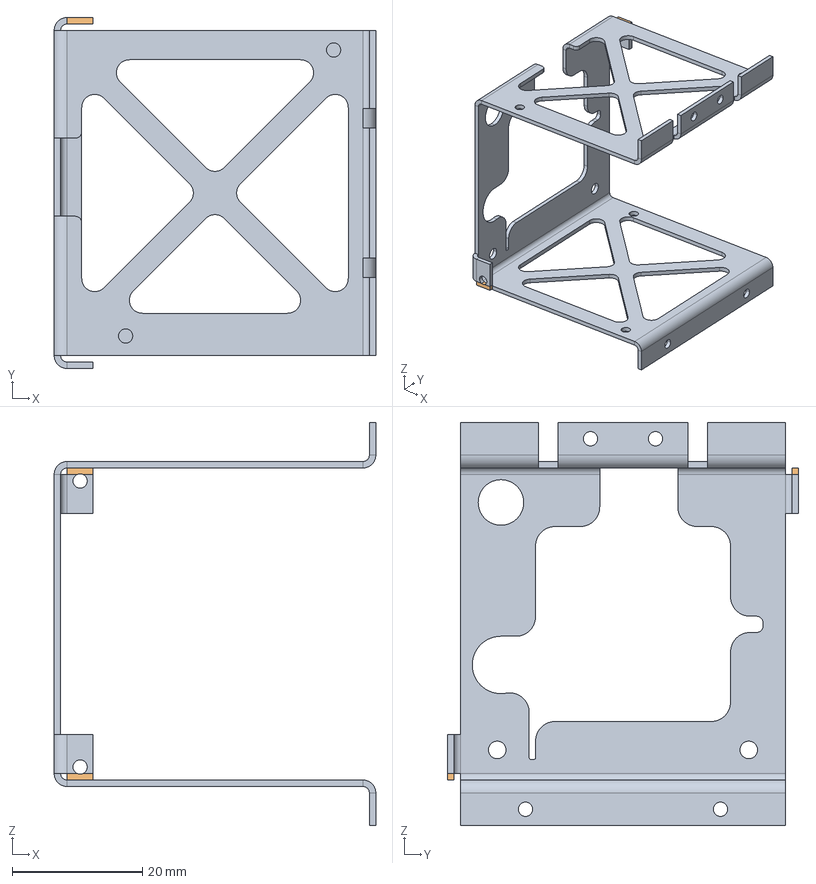
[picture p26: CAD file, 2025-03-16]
CAD/pq-walls-4-5.stp
49.5 x 54.0 x 62.0 mm

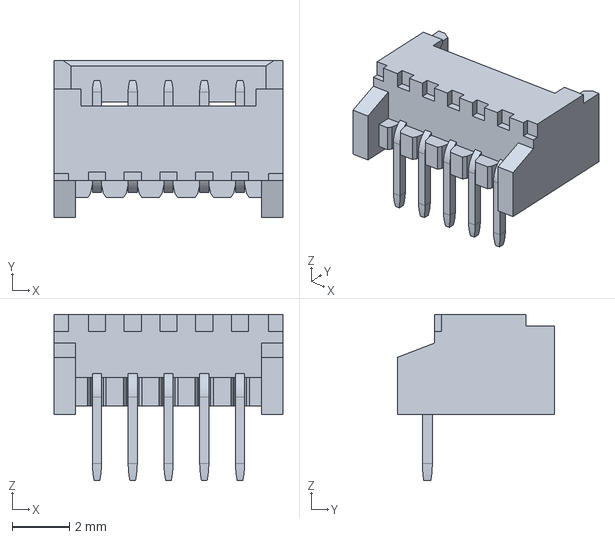
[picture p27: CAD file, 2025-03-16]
CAD/530480510.stp
8.00 x 5.50 x 5.80 mm

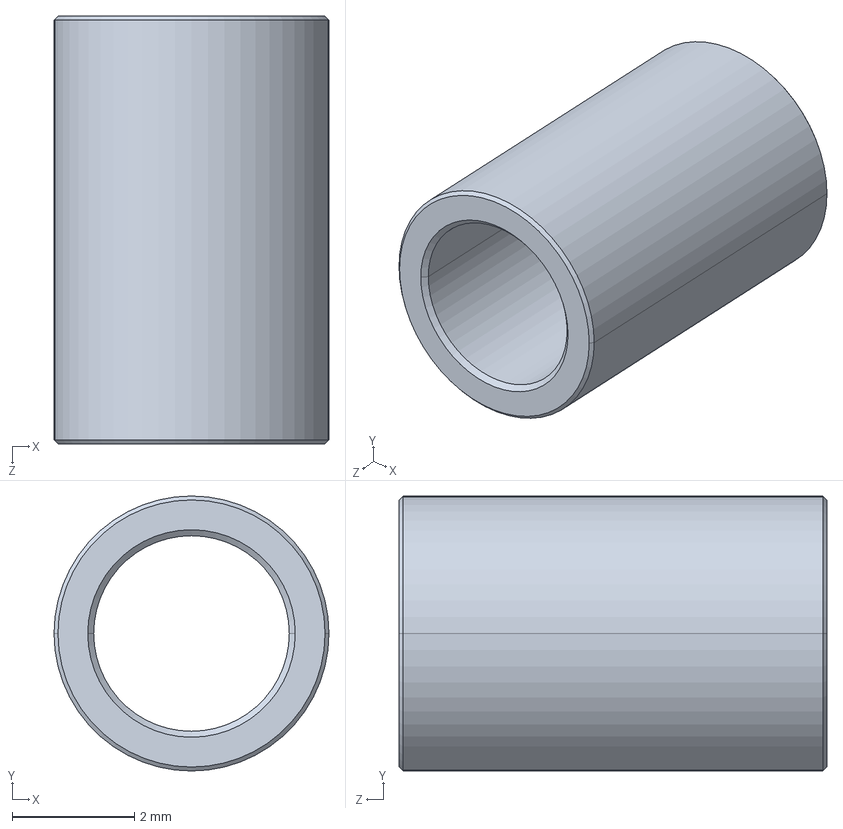
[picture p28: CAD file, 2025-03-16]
CAD/94669A304_Aluminum Unthreaded Spacer.STEP
4.50 x 4.50 x 7.00 mm

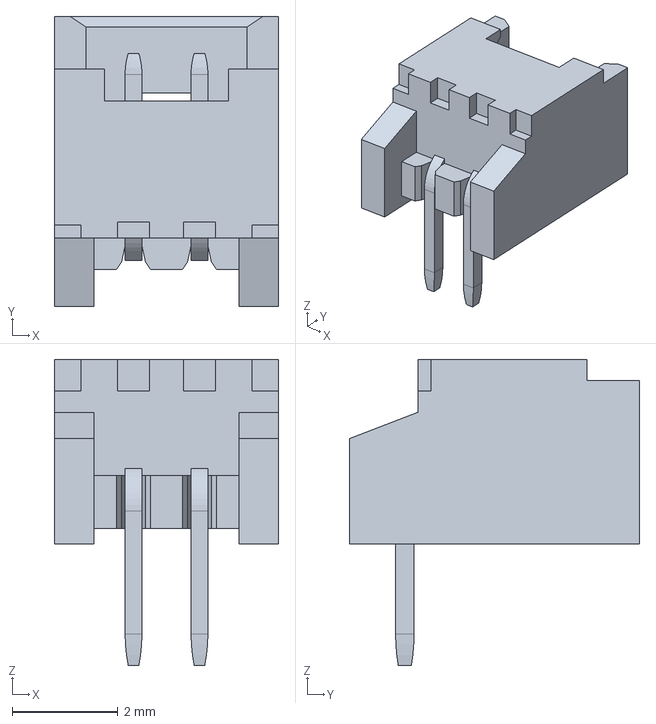
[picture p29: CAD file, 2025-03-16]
CAD/530480210_1_2_3.stp
4.25 x 5.50 x 5.80 mm

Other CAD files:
Backplate/D2F-L2-A.STEP
CAD/PV_Panel_Near.step

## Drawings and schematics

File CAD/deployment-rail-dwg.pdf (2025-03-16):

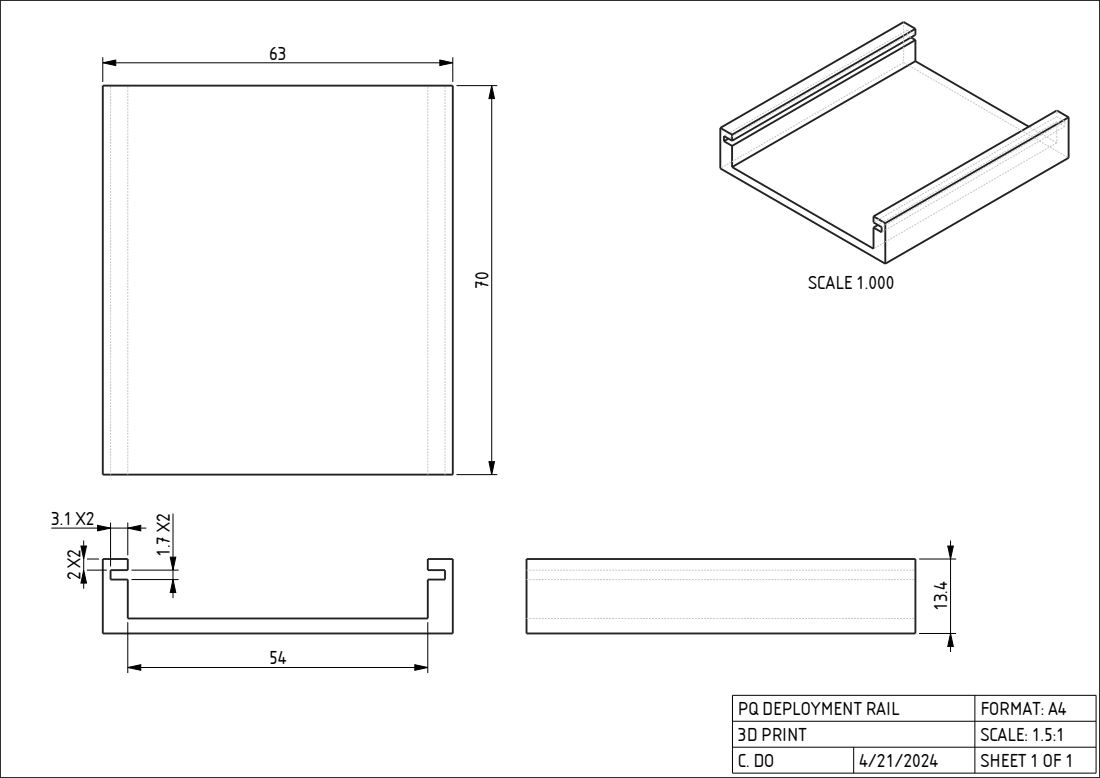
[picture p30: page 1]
SCALE 1.000

PQ DEPLOYMENT RAIL | FORMAT: A4
3D PRINT | SCALE: 1.5:1
C. DO | 4/21/2024 | SHEET 1 OF 1

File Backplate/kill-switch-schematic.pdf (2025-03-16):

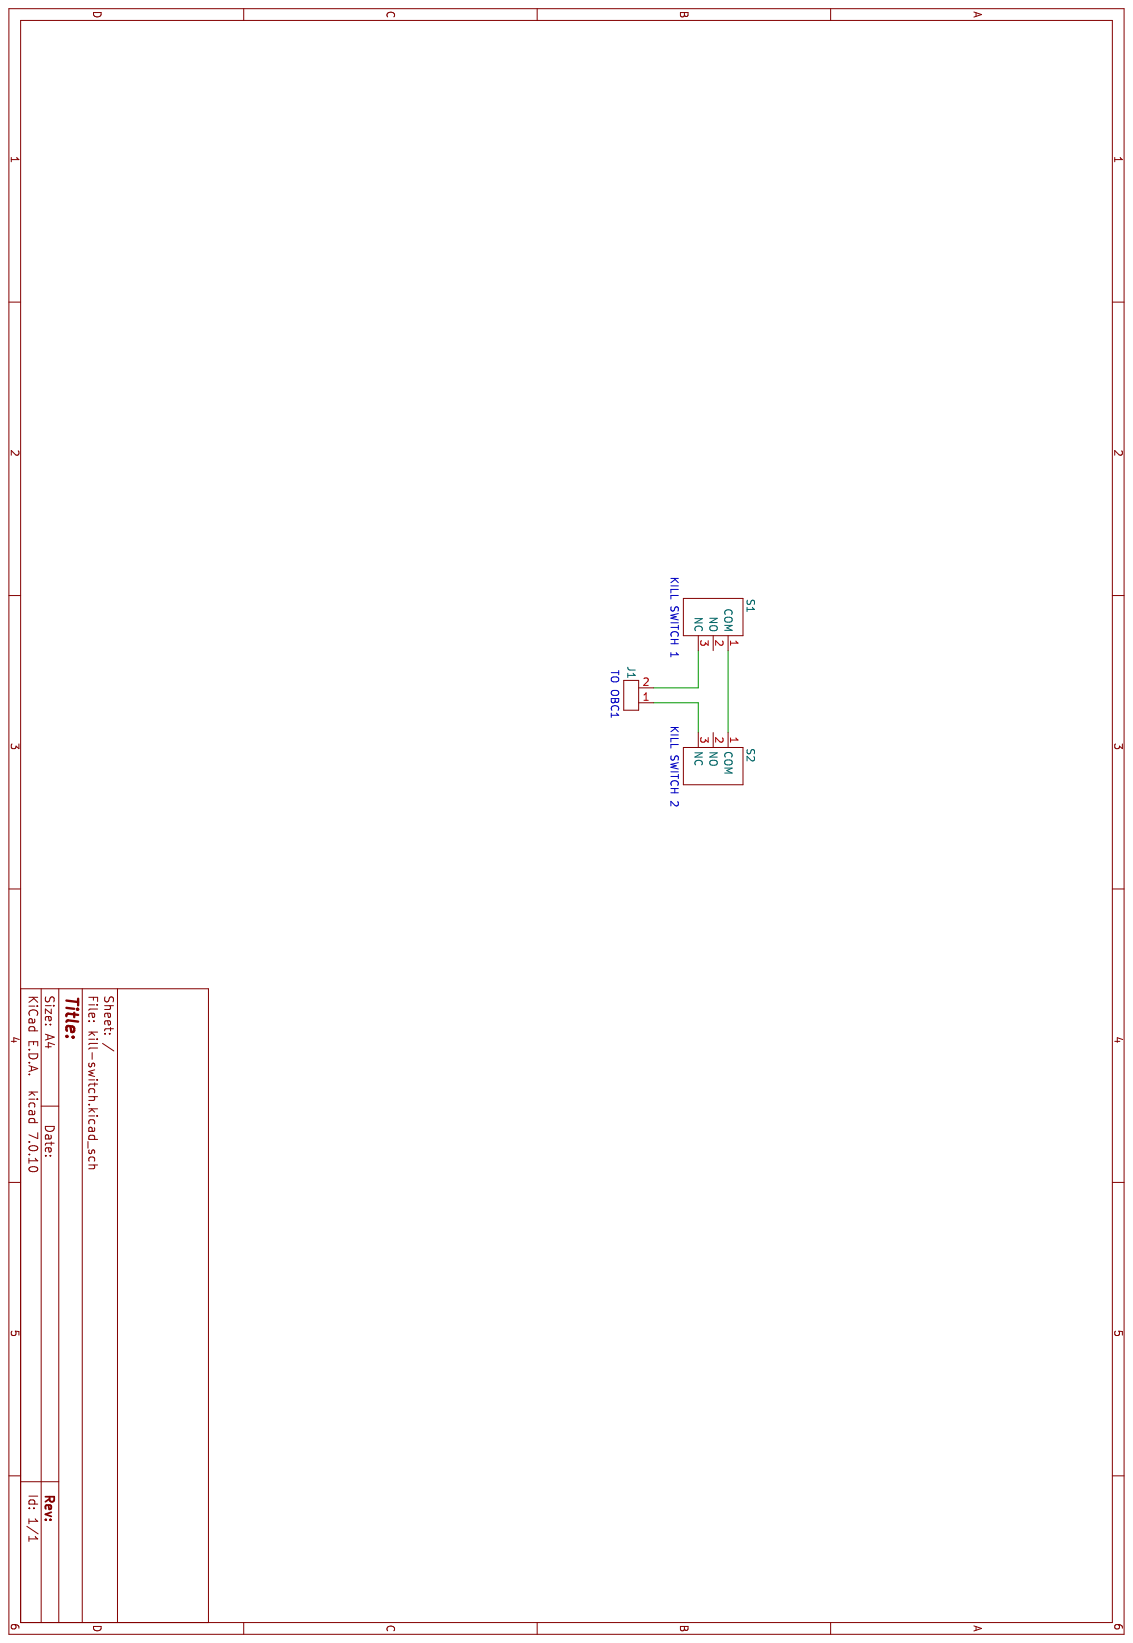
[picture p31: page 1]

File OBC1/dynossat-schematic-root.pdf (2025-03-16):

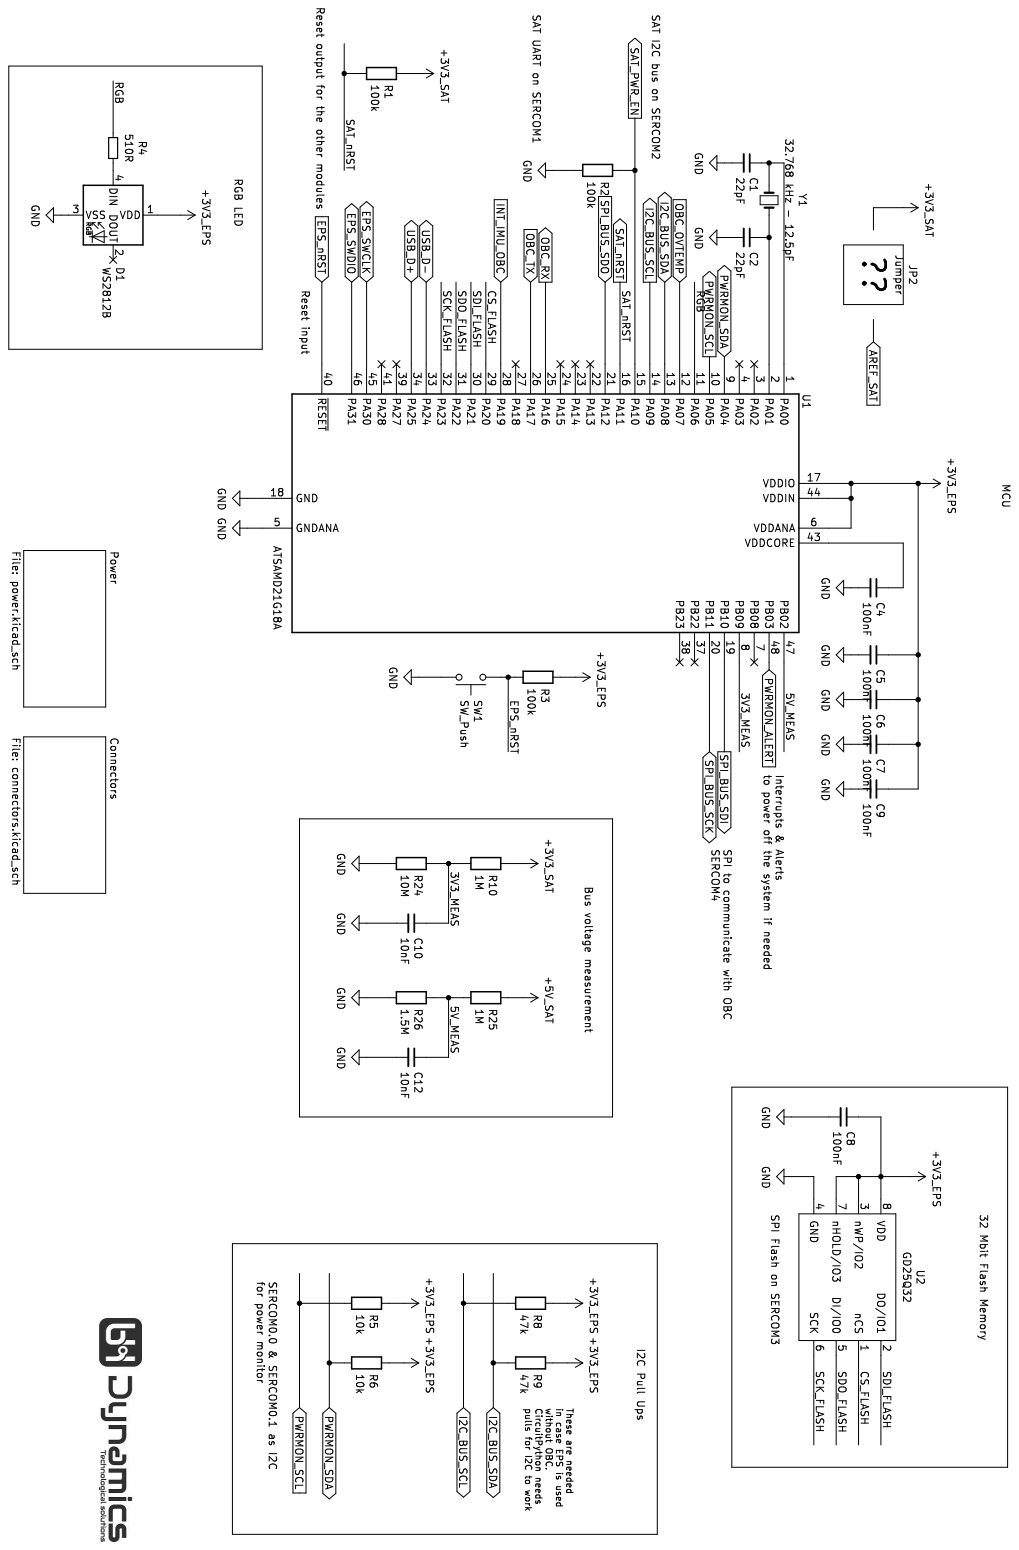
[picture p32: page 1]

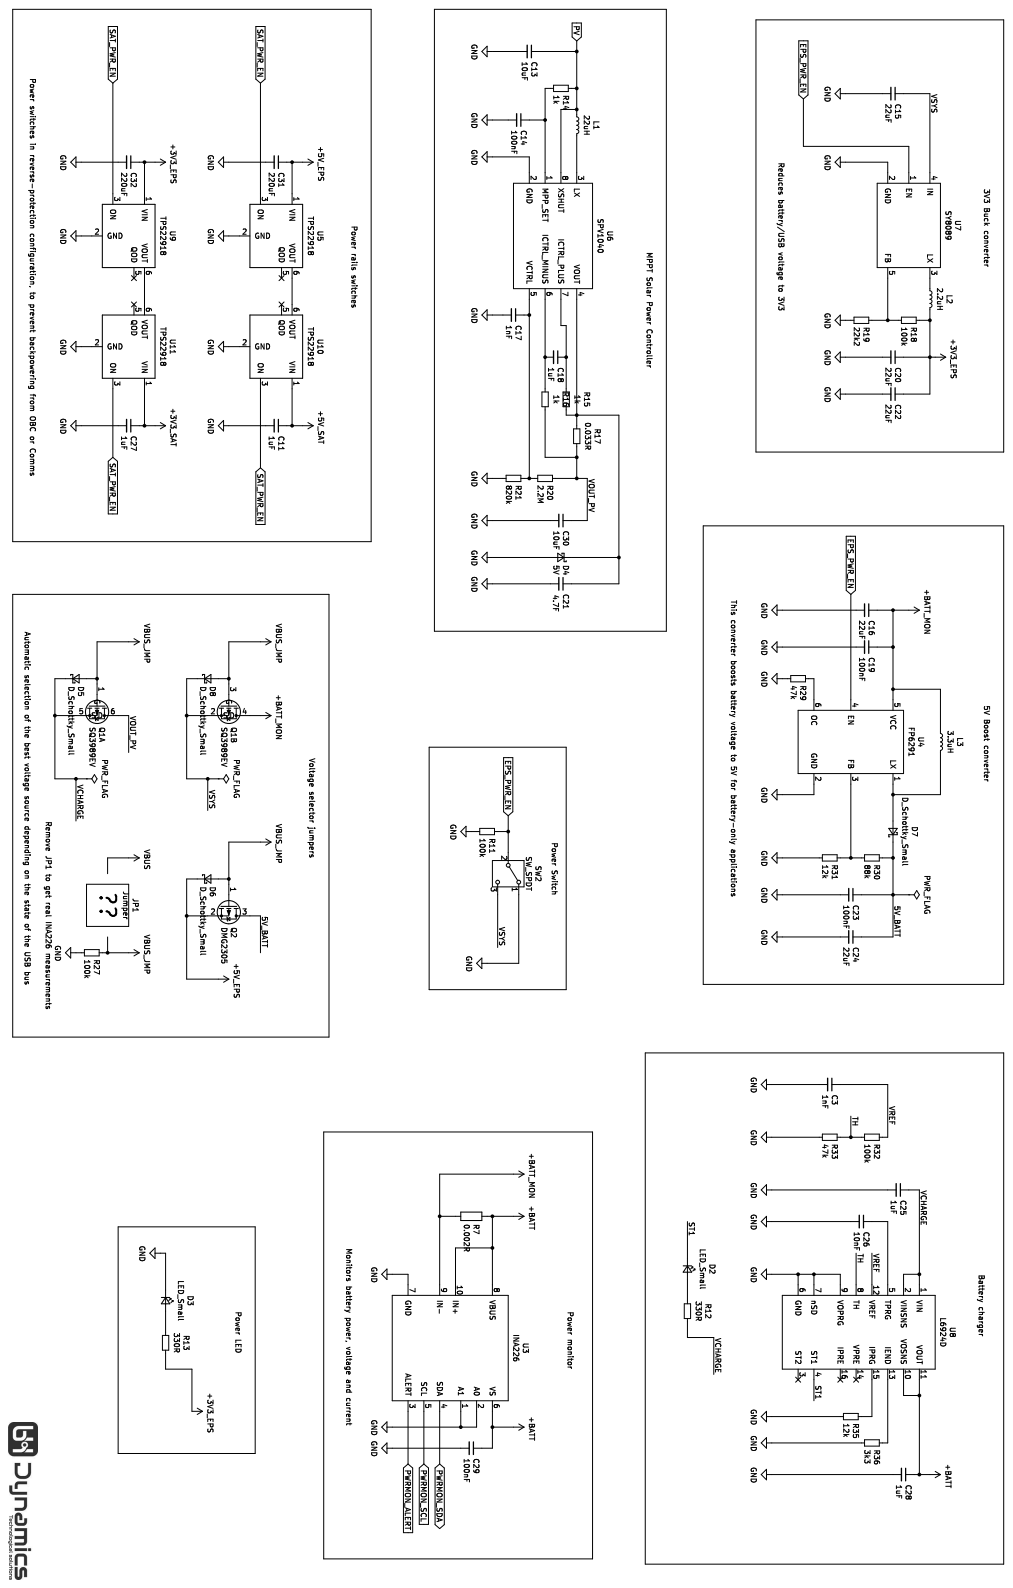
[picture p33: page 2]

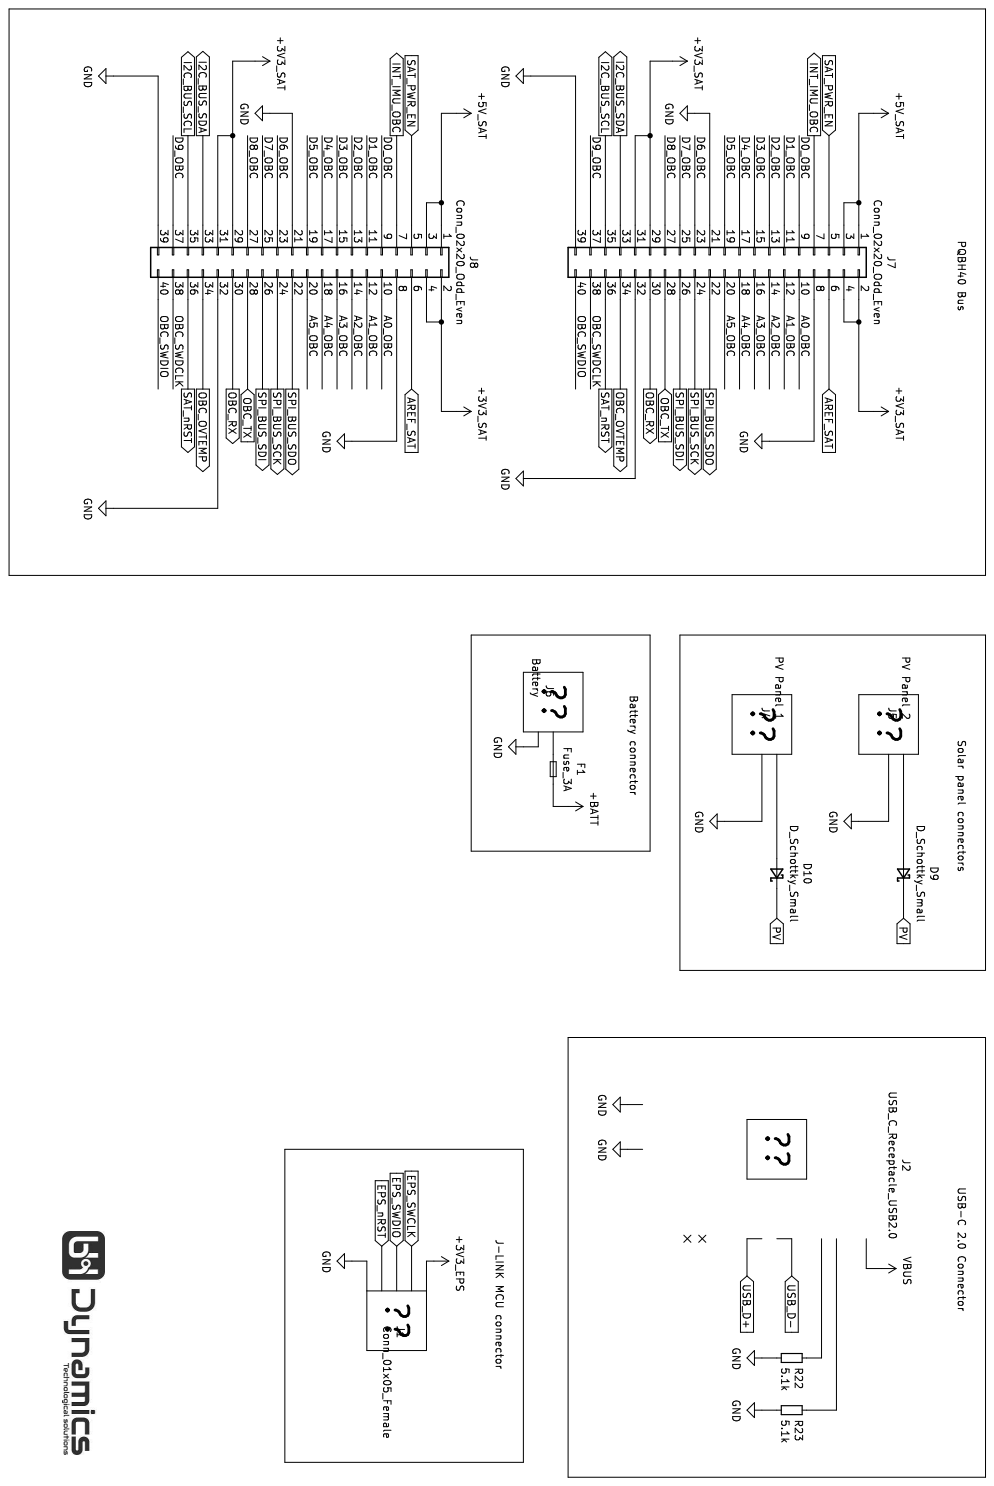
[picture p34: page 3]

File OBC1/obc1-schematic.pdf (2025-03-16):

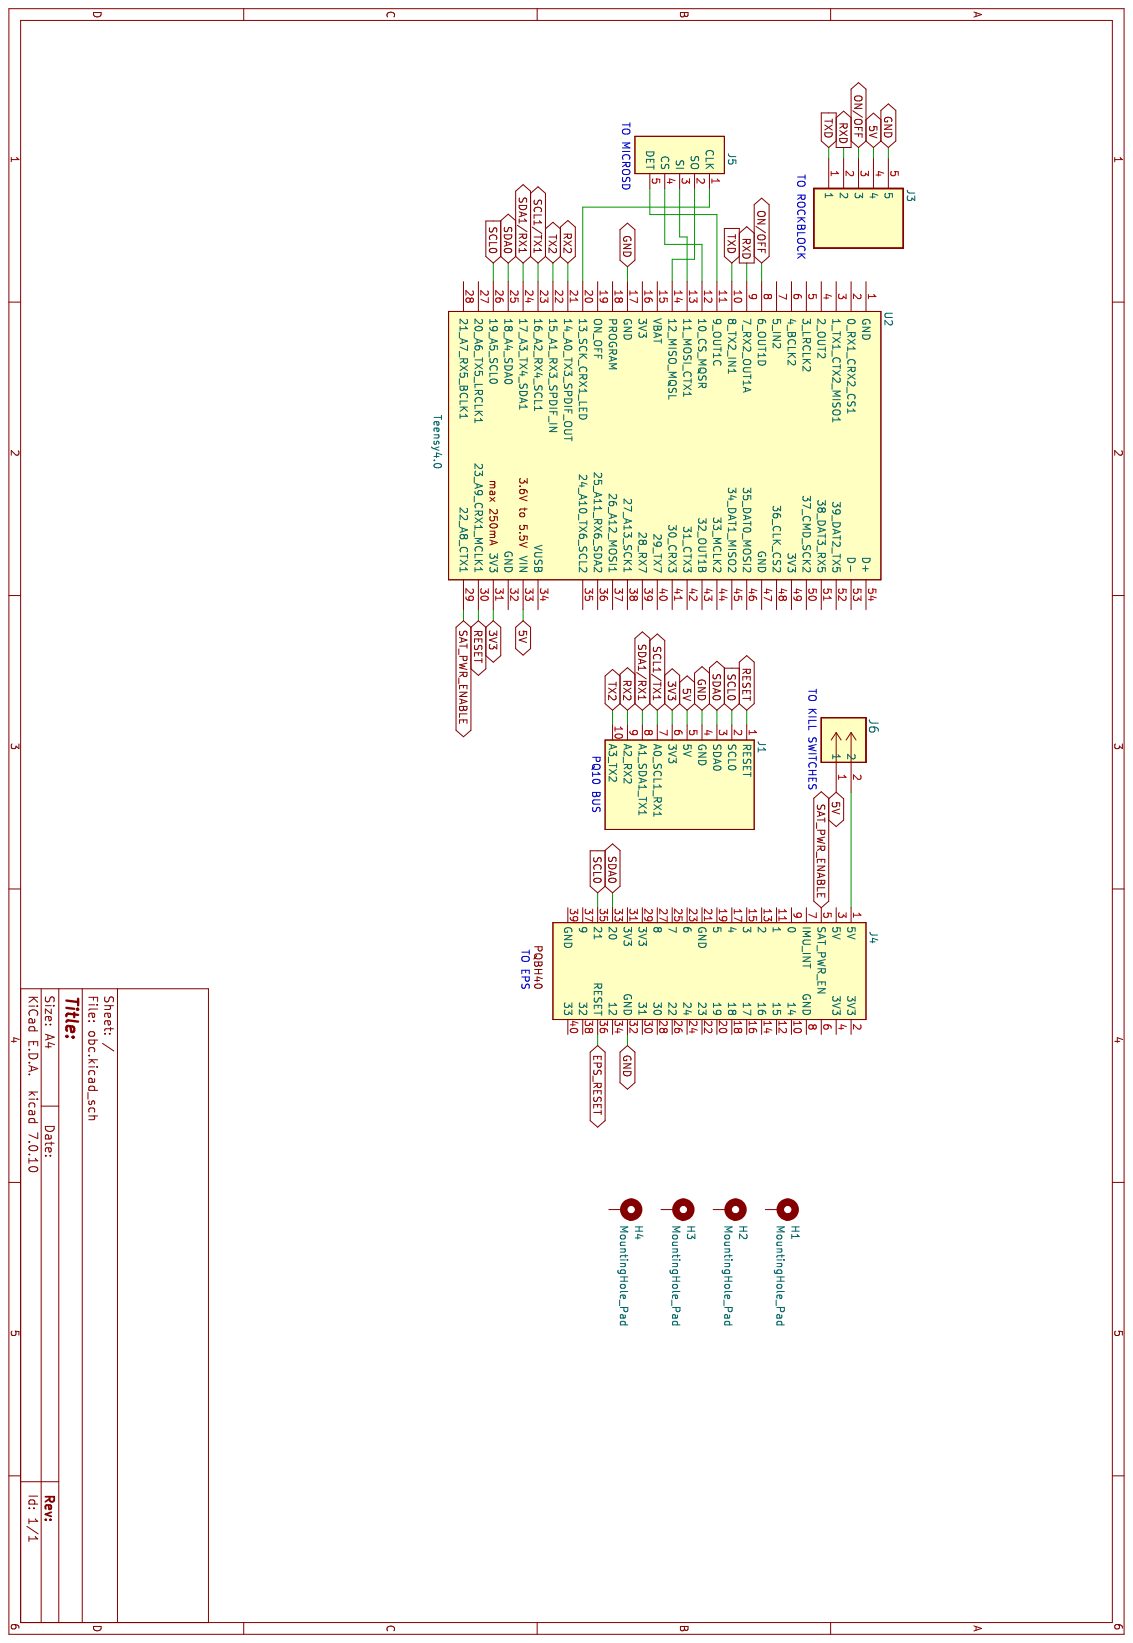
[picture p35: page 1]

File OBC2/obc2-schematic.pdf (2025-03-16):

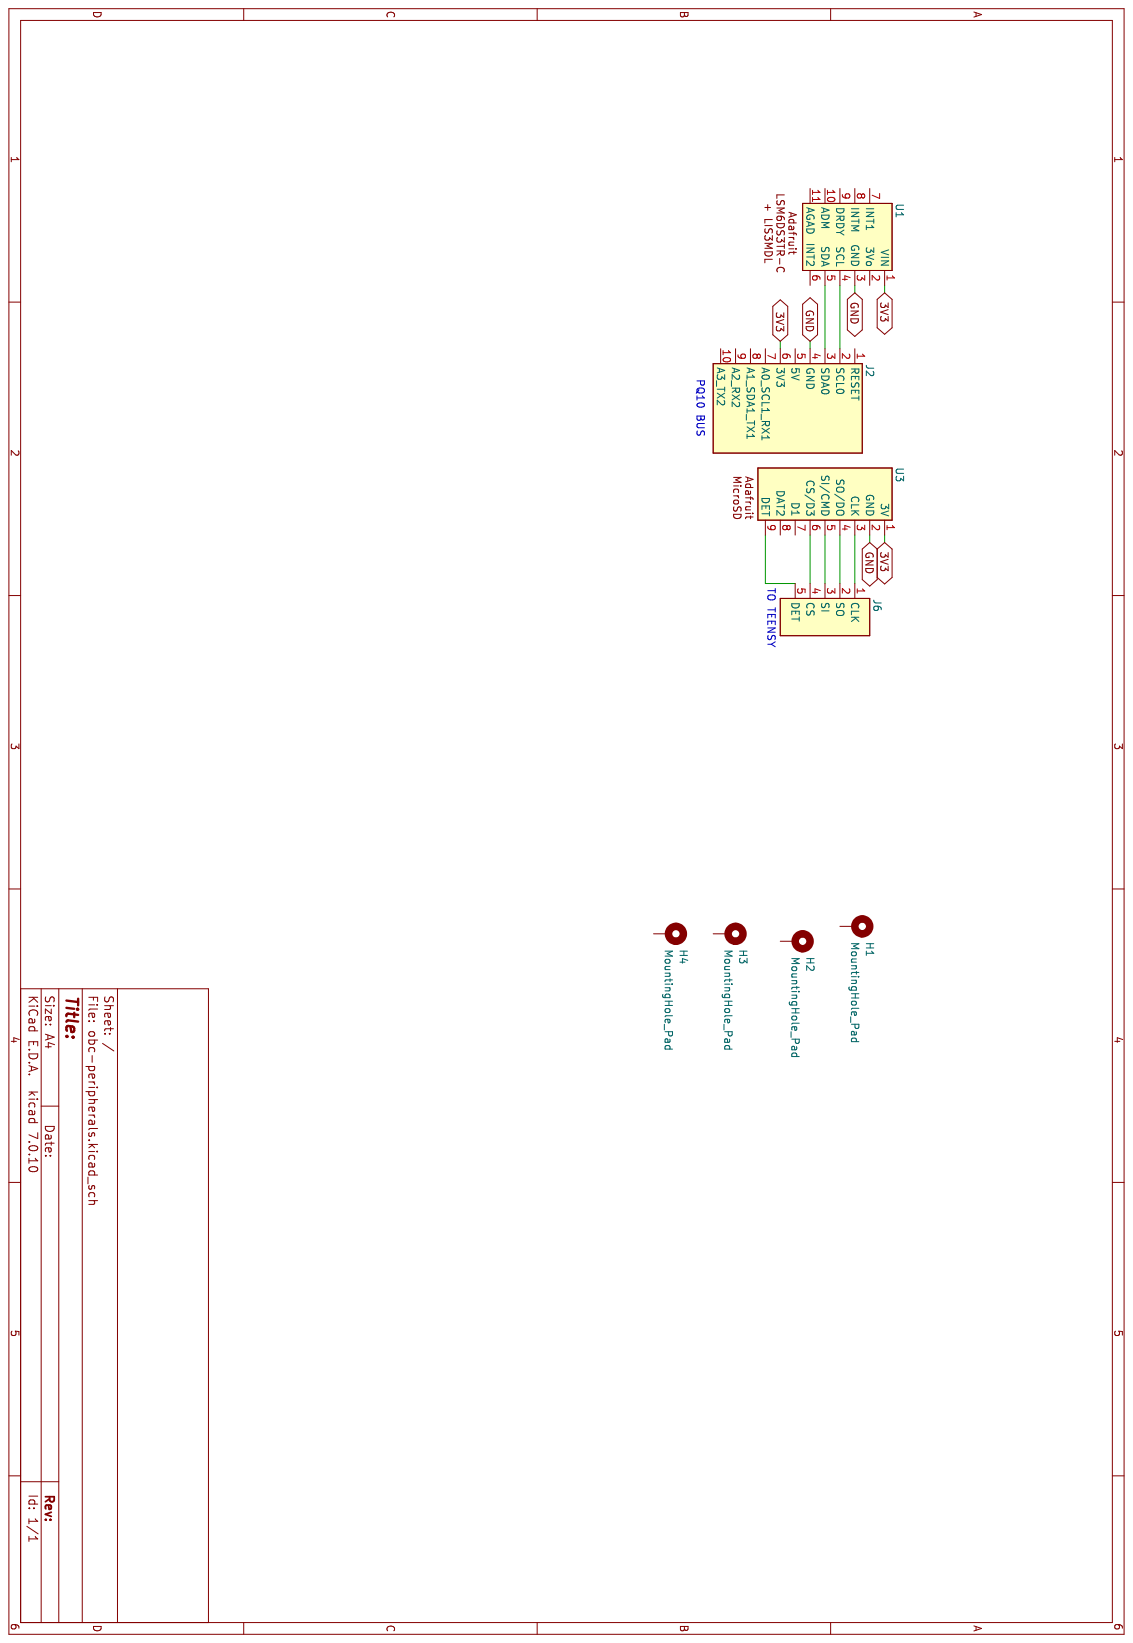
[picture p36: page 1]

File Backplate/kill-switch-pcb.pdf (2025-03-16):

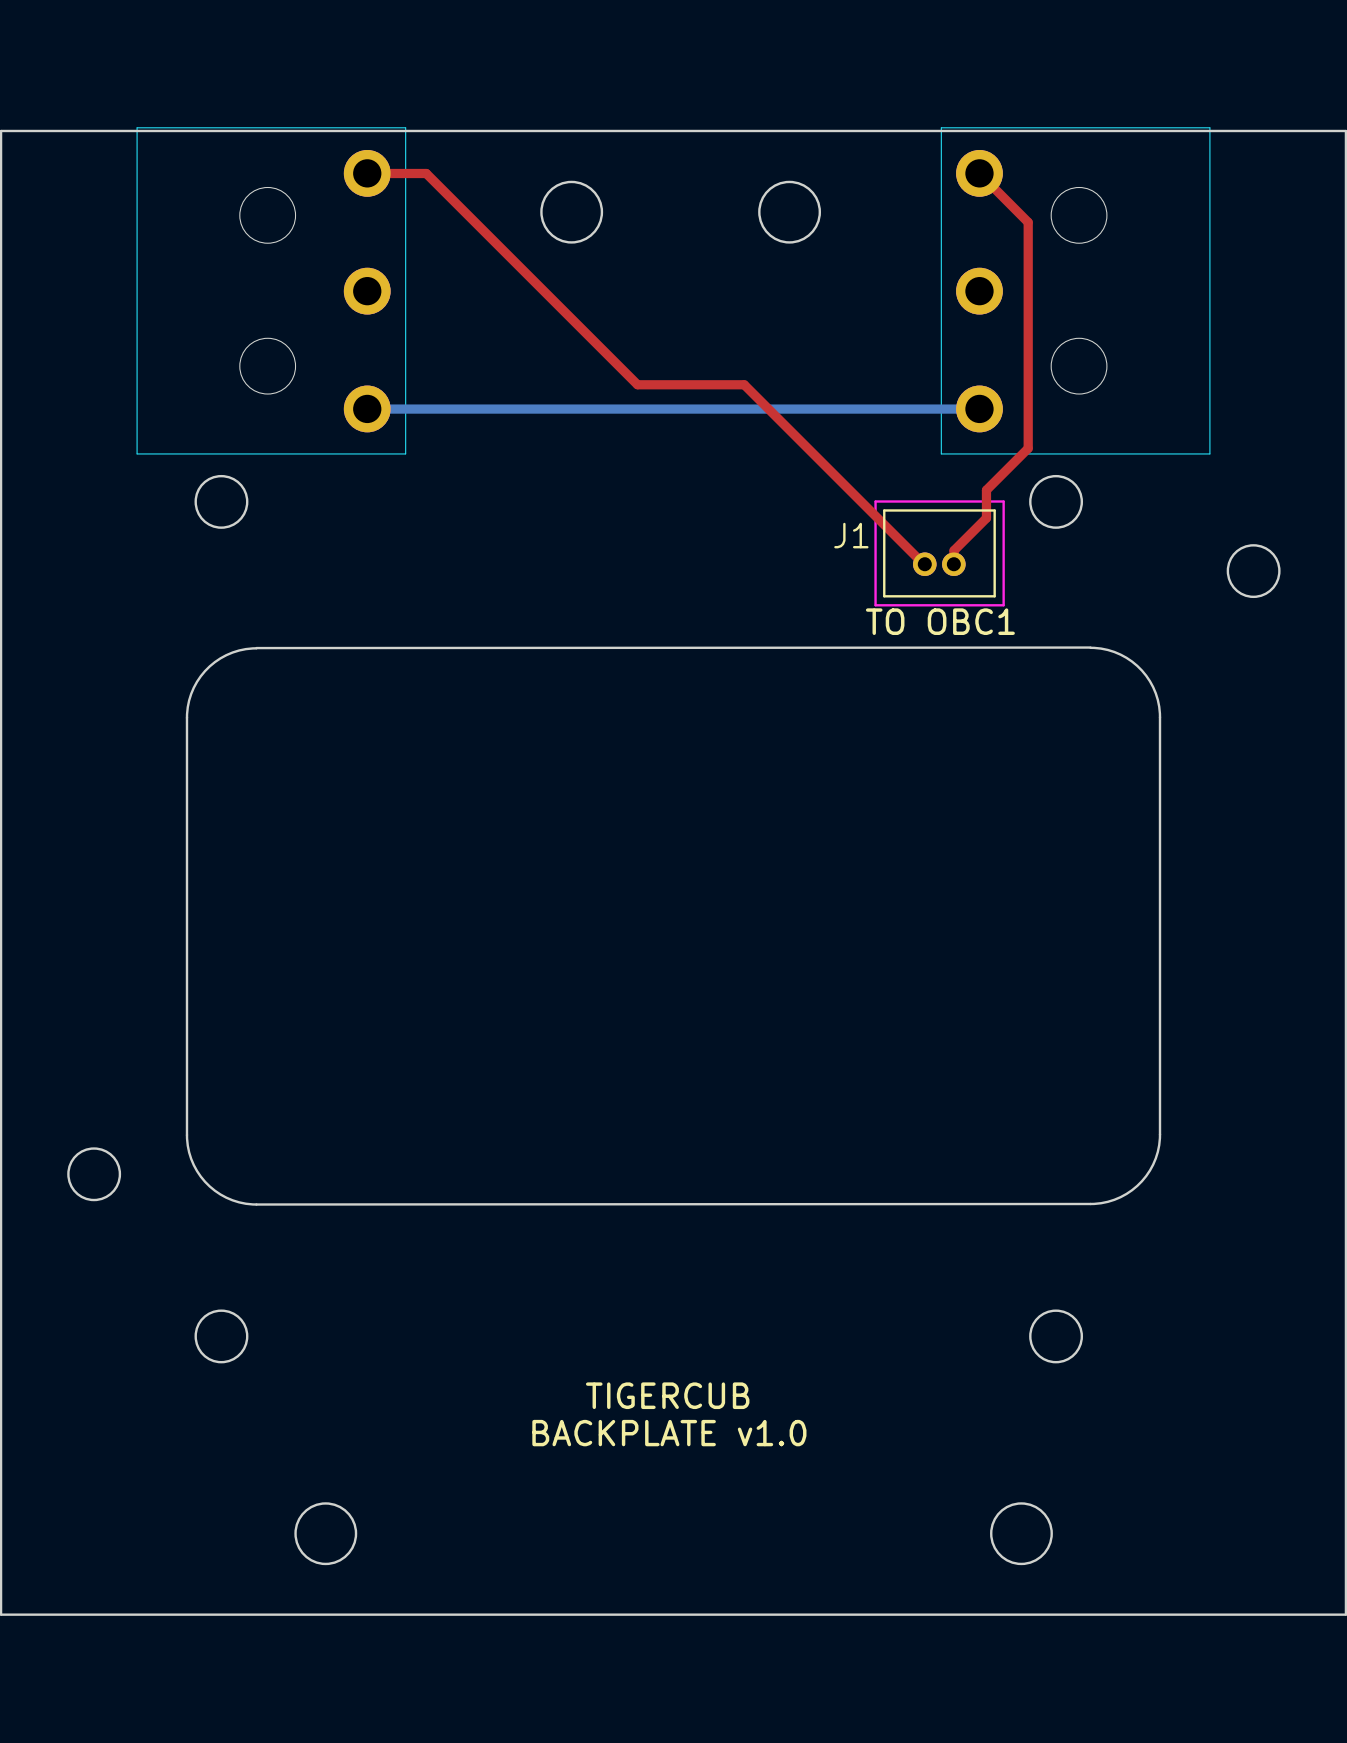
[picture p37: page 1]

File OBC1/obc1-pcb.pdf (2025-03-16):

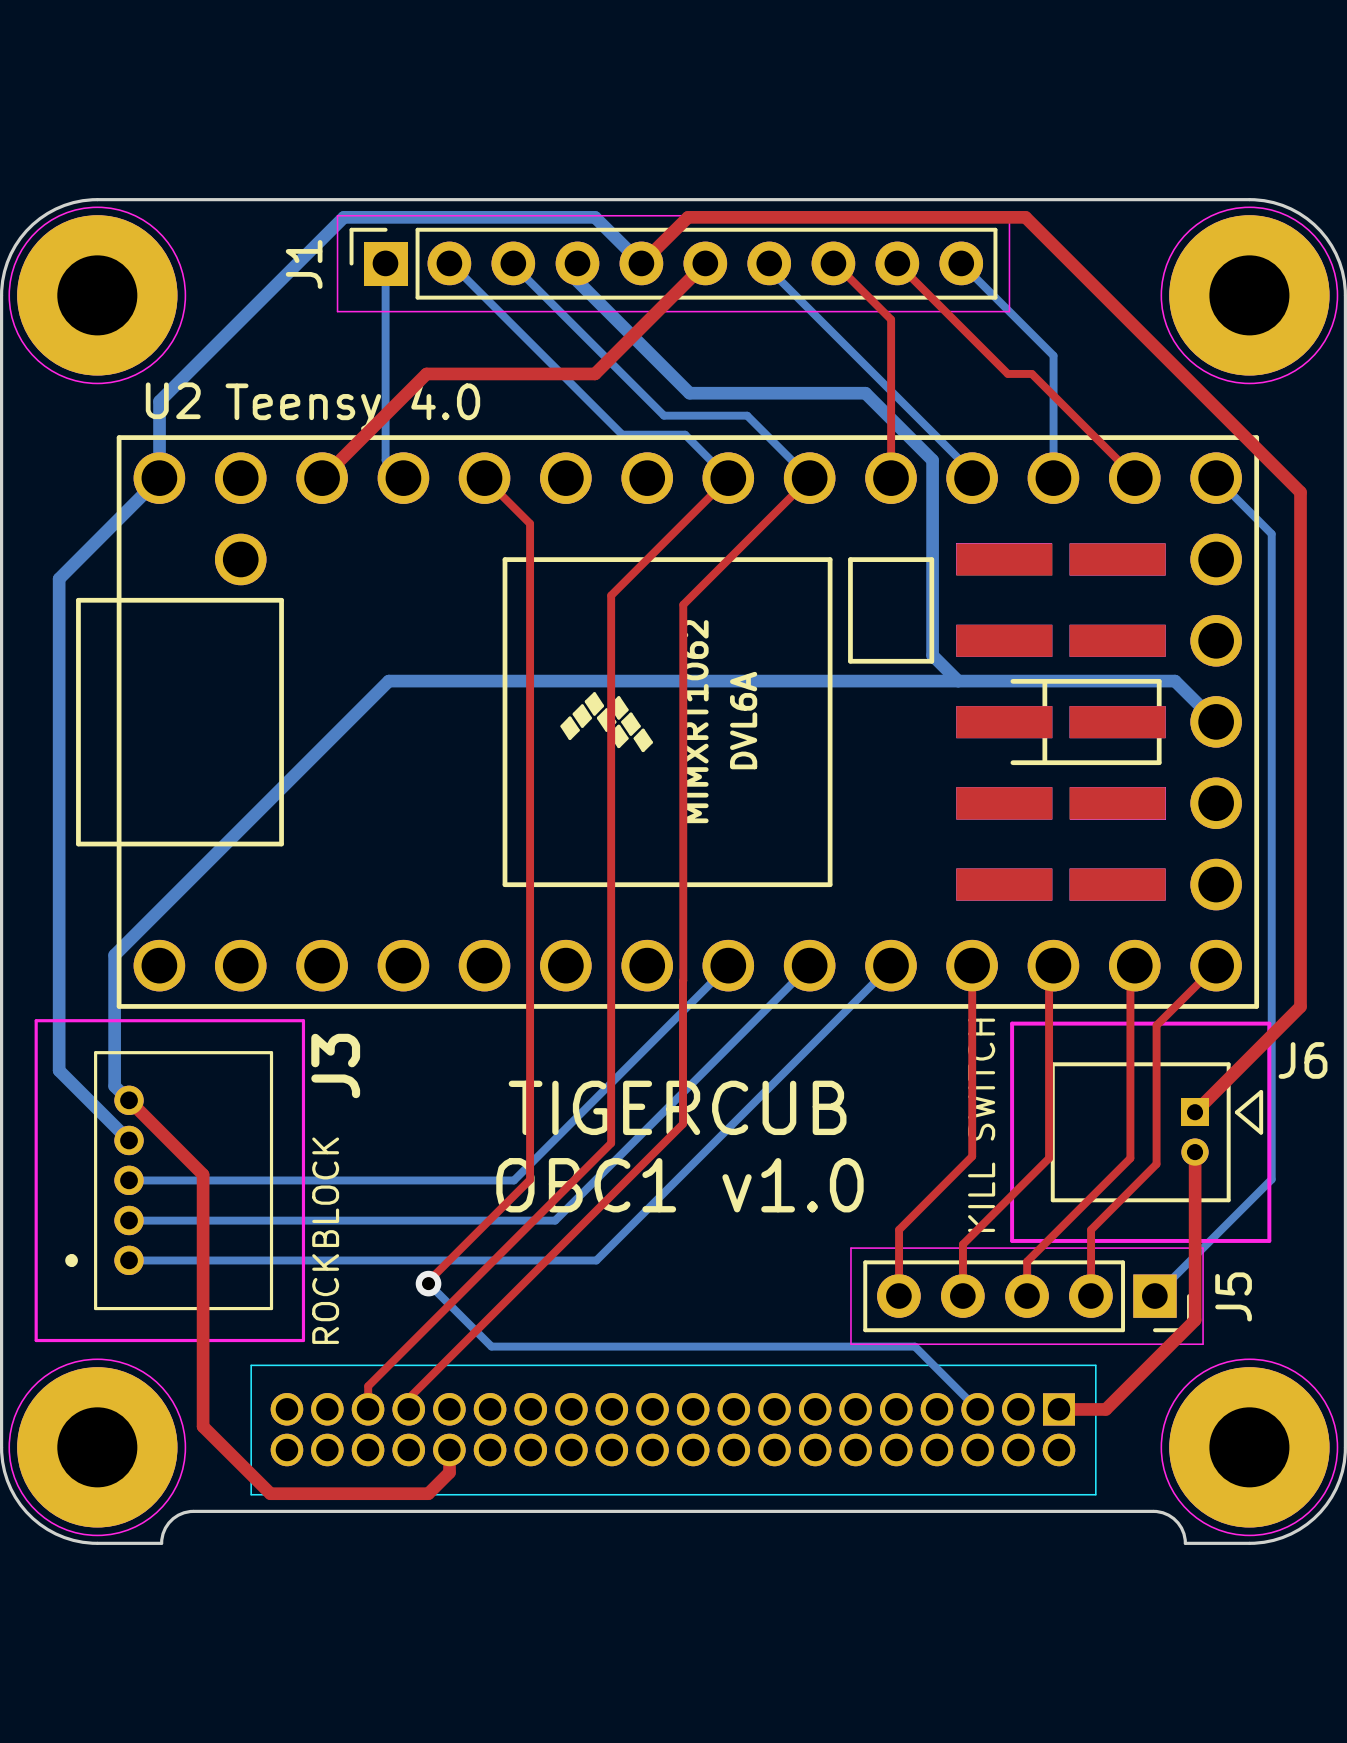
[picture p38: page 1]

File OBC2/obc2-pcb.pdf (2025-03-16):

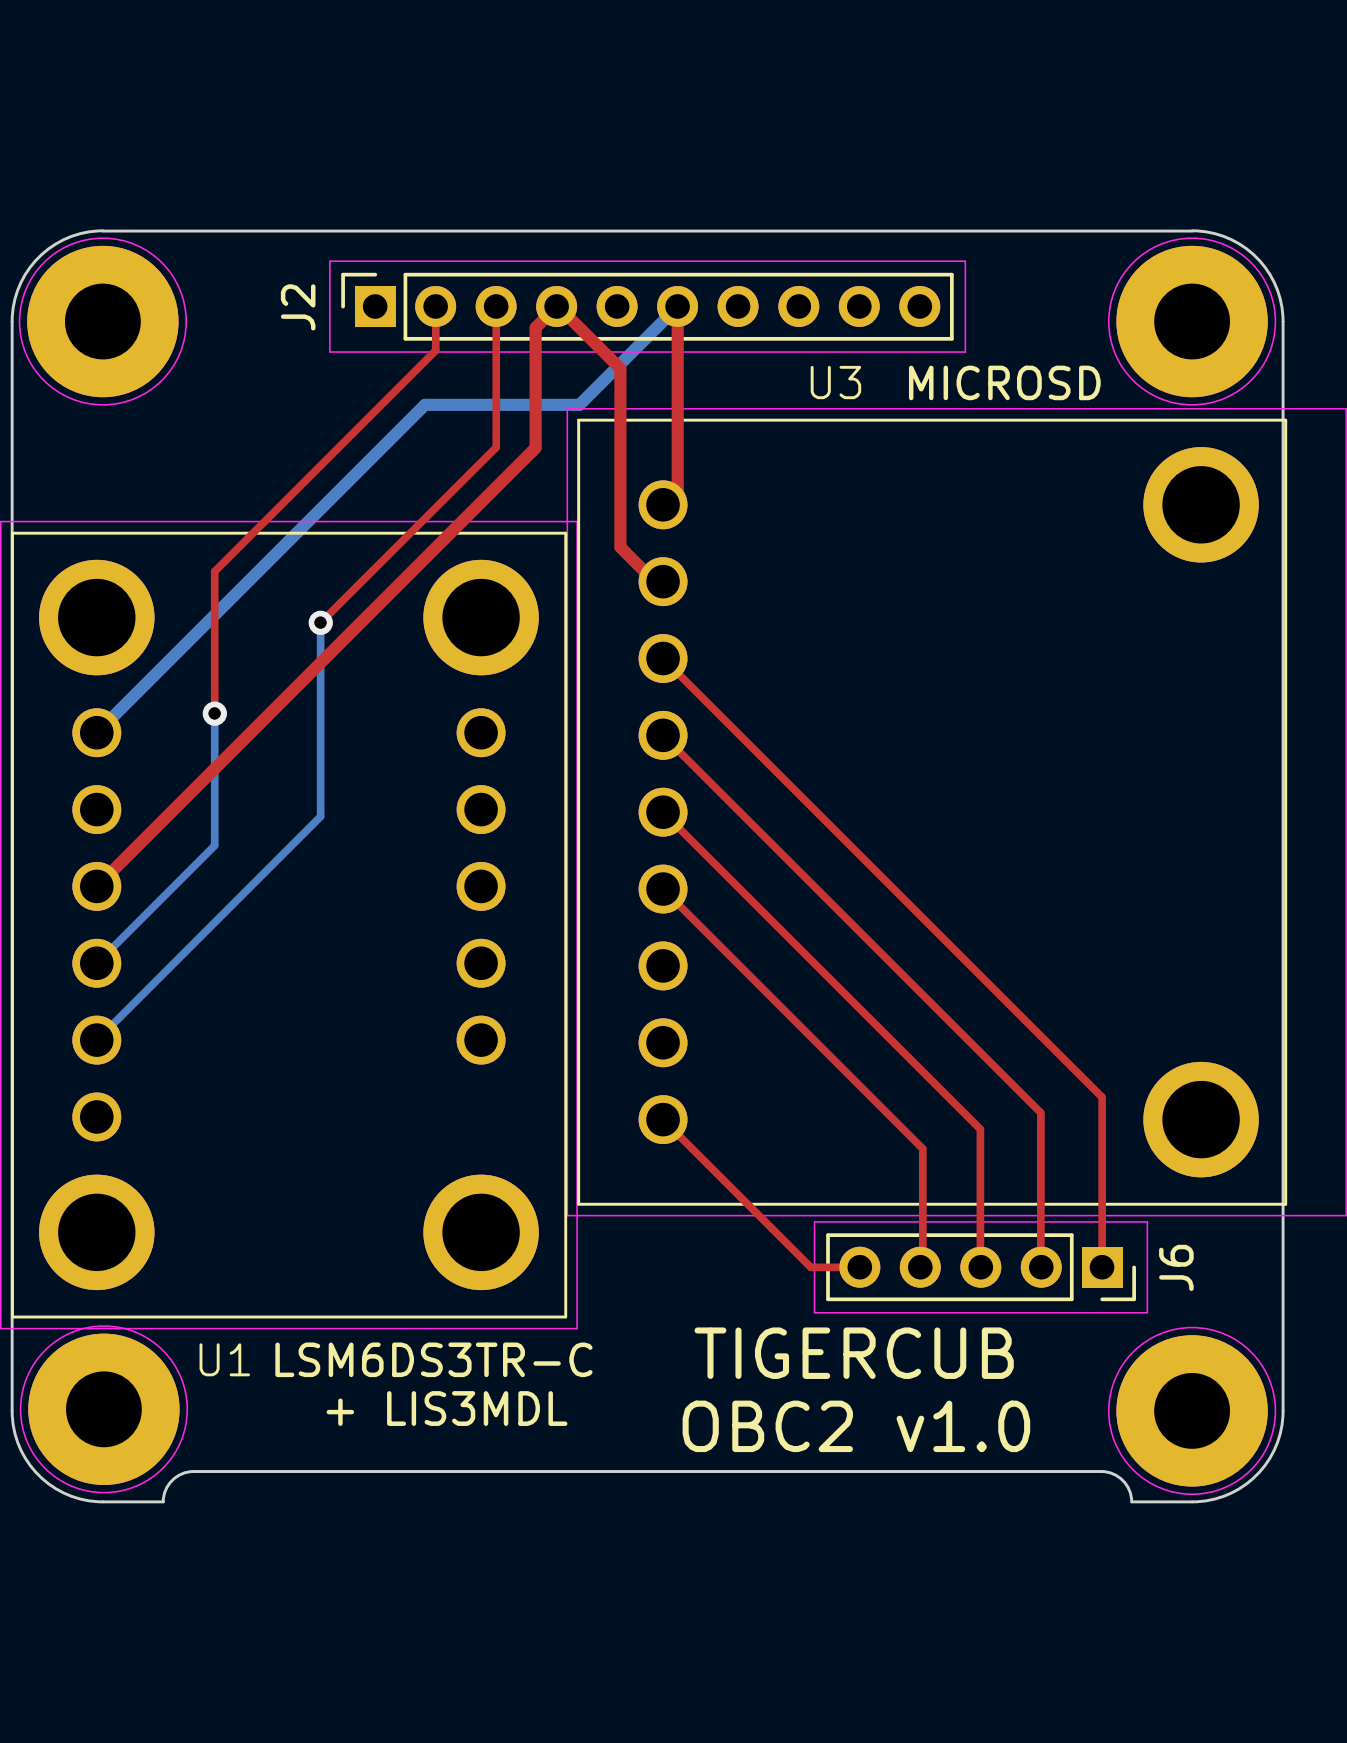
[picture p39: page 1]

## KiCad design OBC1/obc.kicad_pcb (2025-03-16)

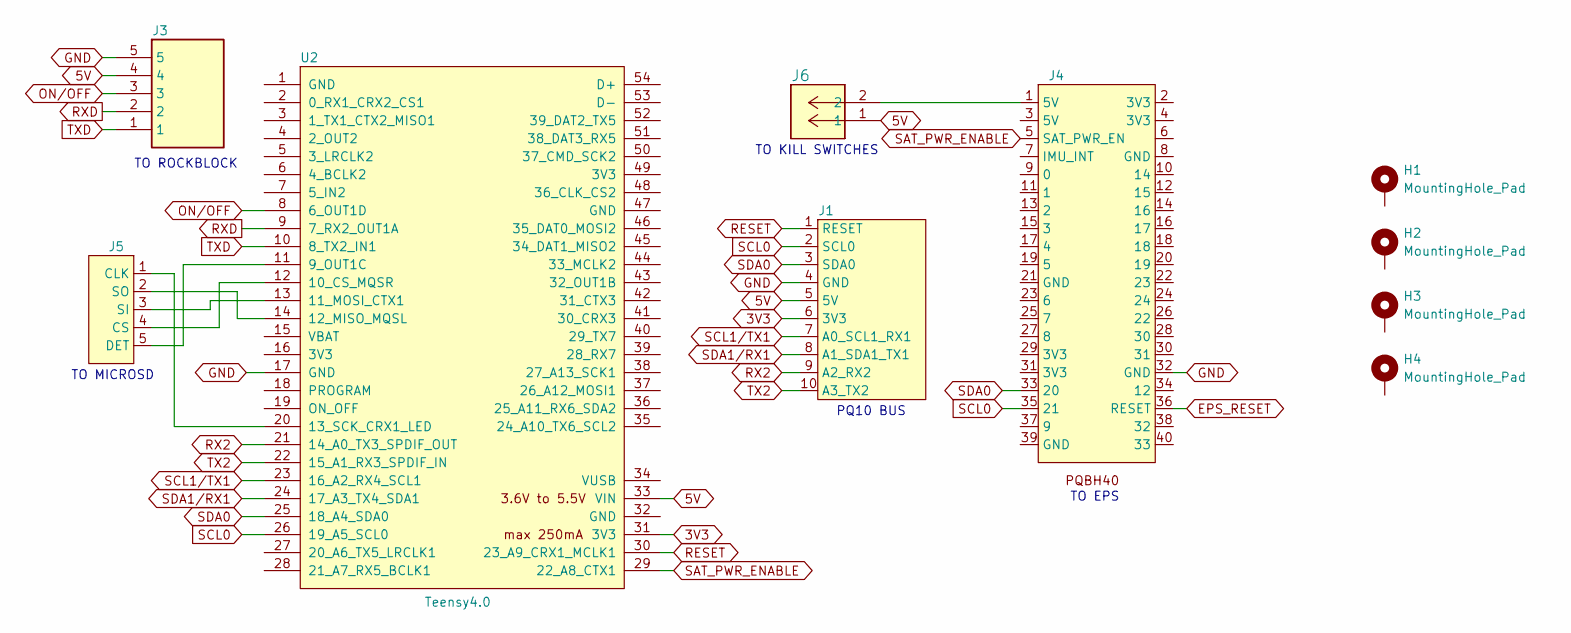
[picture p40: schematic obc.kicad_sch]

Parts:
H1, H2, H3, H4: MountingHole_Pad; MountingHole_2.5mm_Pad
J1: PinSocket_1x10_P2.00mm_Vertical
J2: (no value)
J3: 53048-0510; 530480510; Mouser Part Number 538-53048-0510
J4: PinSocket_2x20_P1.27mm_Vertical
J5: PinSocket_1x05_P2.00mm_Vertical
J6: 530480210; Molex_Picoblade_2x1_horz
U2: Teensy4.0; Teensy40

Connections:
3V3: J1.6 (3V3), U2.31 (3V3)
5V: J1.5 (5V), J3.4, J6.1, U2.33 (VIN)
EPS_RESET: J4.36 (RESET)
GND: J1.4 (GND), J3.5, J4.32 (GND), U2.17 (GND)
unnamed: J4.1 (5V), J6.2
unnamed: J5.1 (CLK), U2.20 (13_SCK_CRX1_LED)
unnamed: J5.4 (CS), U2.12 (10_CS_MQSR)
unnamed: J5.5 (DET), U2.11 (9_OUT1C)
unnamed: J5.3 (SI), U2.13 (11_MOSI_CTX1)
unnamed: J5.2 (SO), U2.14 (12_MISO_MQSL)
ON/OFF: J3.3, U2.8 (6_OUT1D)
RESET: J1.1 (RESET), U2.30 (23_A9_CRX1_MCLK1)
RX2: J1.9 (A2_RX2), U2.21 (14_A0_TX3_SPDIF_OUT)
RXD: J3.2, U2.9 (7_RX2_OUT1A)
SAT_PWR_ENABLE: J4.5 (SAT_PWR_EN), U2.29 (22_A8_CTX1)
SCL0: J1.2 (SCL0), J4.35 (21), U2.26 (19_A5_SCL0)
SCL1/TX1: J1.7 (A0_SCL1_RX1), U2.23 (16_A2_RX4_SCL1)
SDA0: J1.3 (SDA1), J4.33 (20), U2.25 (18_A4_SDA0)
SDA1/RX1: J1.8 (A1_SDA1_TX1), U2.24 (17_A3_TX4_SDA1)
TX2: J1.10 (A3_TX2), U2.22 (15_A1_RX3_SPDIF_IN)
TXD: J3.1, U2.10 (8_TX2_IN1)

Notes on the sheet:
TO KILL SWITCHES
PQ10 BUS
TO ROCKBLOCK
TO EPS
TO MICROSD

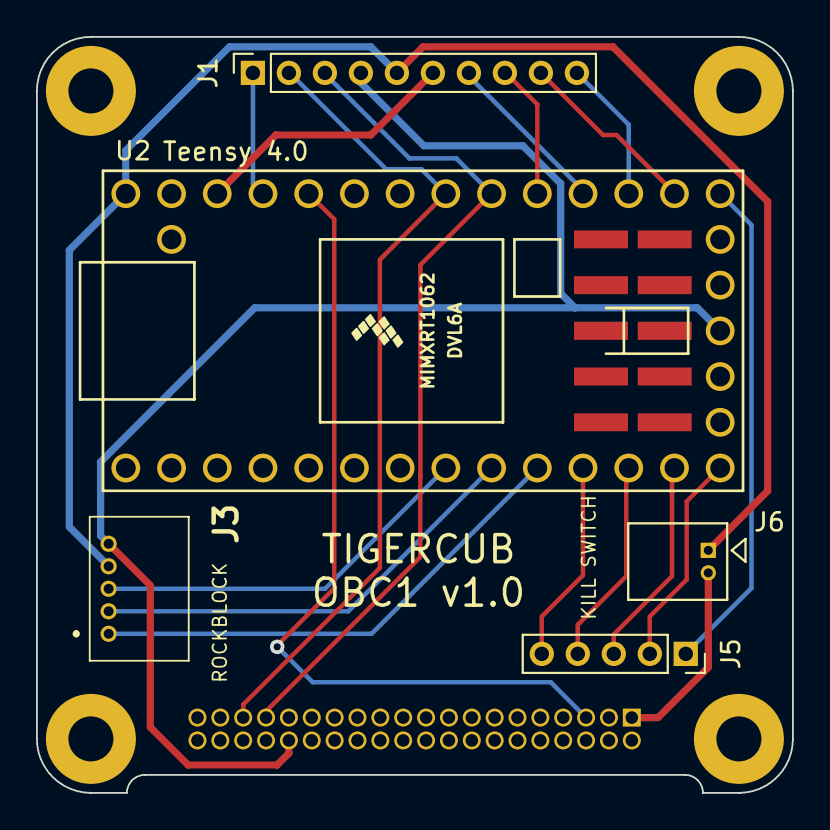
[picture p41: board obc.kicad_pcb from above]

Board: 2 copper layers, 42.0 x 42.0 mm, 10 parts (1 on the bottom side), 20 nets.

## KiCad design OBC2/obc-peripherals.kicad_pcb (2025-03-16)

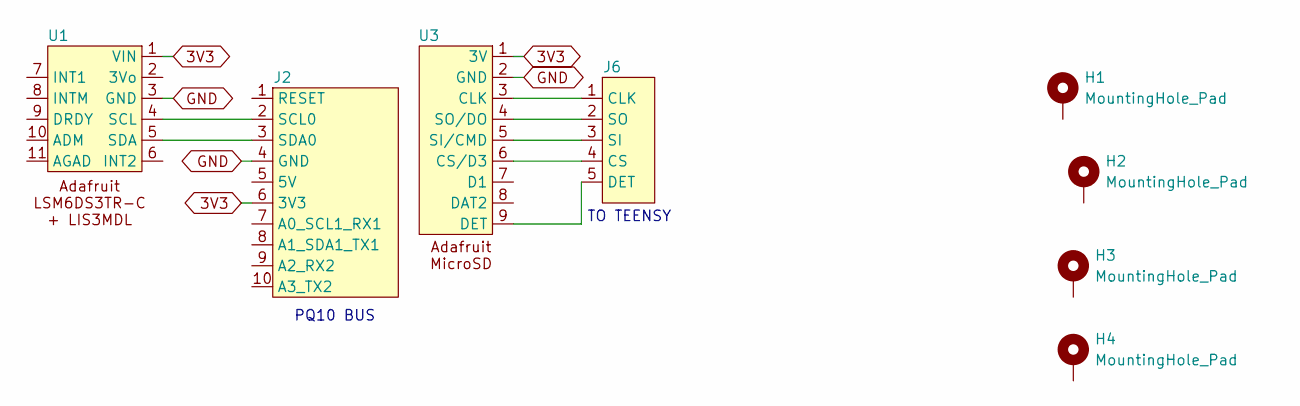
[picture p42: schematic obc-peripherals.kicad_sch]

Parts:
H1, H2, H3, H4: MountingHole_Pad; MountingHole_2.5mm_Pad
J2: PinSocket_1x10_P2.00mm_Vertical
J6: PinSocket_1x05_P2.00mm_Vertical
U1: Adafruit_LSM6DS3TR-C_LIS3MDL
U3: Adafruit_MicroSD

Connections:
unnamed: J2.6 (3V3), U1.1 (VIN), U3.1 (3V)
unnamed: J2.4 (GND), U1.3 (GND), U3.2 (GND)
unnamed: J2.2 (SCL0), U1.4 (SCL)
unnamed: J2.3 (SDA1), U1.5 (SDA)
unnamed: J6.1 (CLK), U3.3 (CLK)
unnamed: J6.4 (CS), U3.6 (CS/D3)
unnamed: J6.5 (DET), U3.9 (DET)
unnamed: J6.3 (SI), U3.5 (SI/CMD)
unnamed: J6.2 (SO), U3.4 (SO/DO)

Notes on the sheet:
PQ10 BUS
TO TEENSY

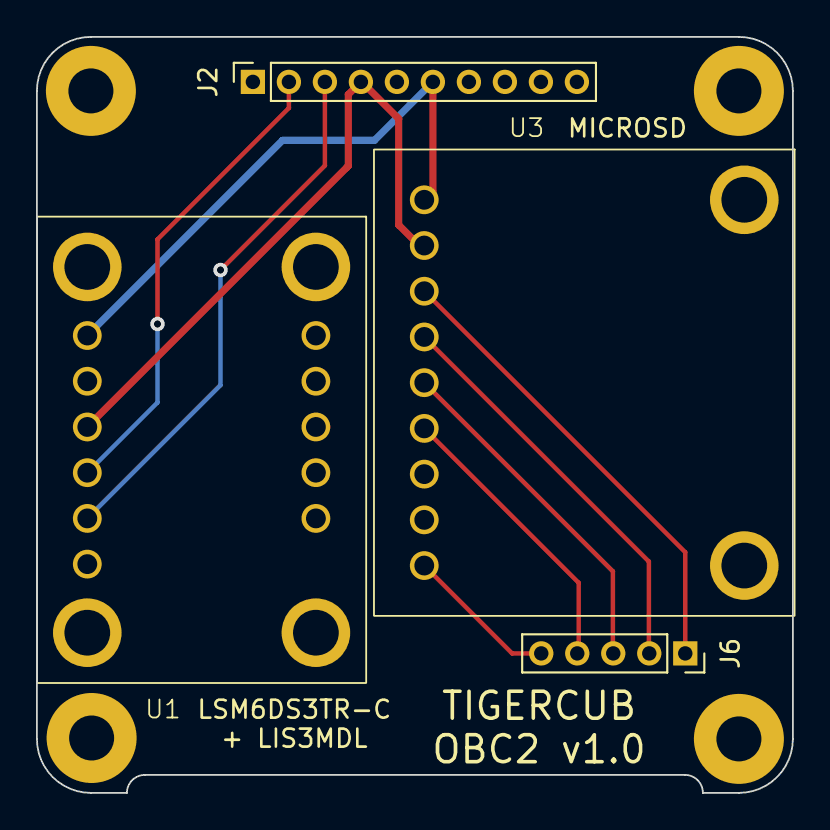
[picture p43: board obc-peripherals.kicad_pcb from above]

Board: 2 copper layers, 42.0 x 42.0 mm, 8 parts (0 on the bottom side), 9 nets.

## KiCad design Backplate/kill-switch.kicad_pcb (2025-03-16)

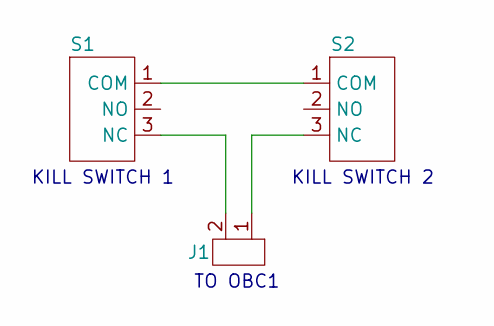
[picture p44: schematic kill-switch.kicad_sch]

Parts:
J1: Molex_Picoblade_2x1_vert
S1: D2F-L2-A
S2: D2F-L2-A1

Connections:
unnamed: S1.1 (COM), S2.1 (COM)
unnamed: J1.2, S1.3 (NC)
unnamed: J1.1, S2.3 (NC)

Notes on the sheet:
KILL SWITCH 1
TO OBC1
KILL SWITCH 2

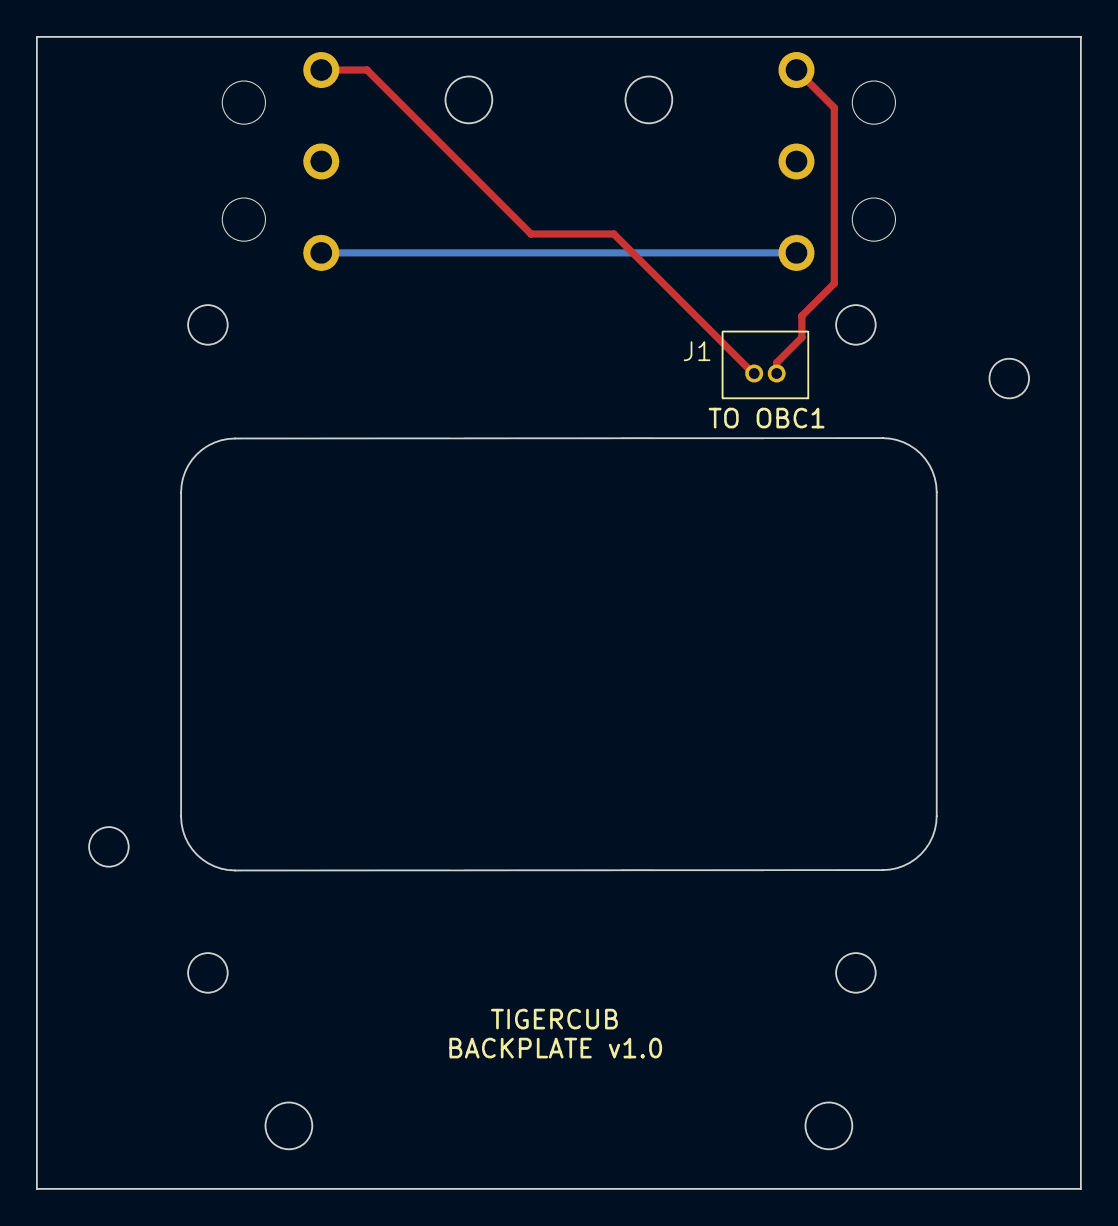
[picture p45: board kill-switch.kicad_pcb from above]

Board: 2 copper layers, 58.0 x 64.0 mm, 3 parts (0 on the bottom side), 3 nets.

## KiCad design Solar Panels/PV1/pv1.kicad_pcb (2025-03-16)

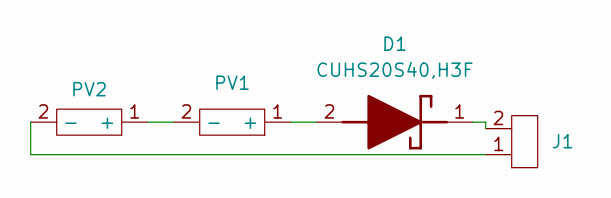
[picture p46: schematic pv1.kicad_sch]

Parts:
D1: CUHS20S40,H3F; CUHS20S40H3F; Mouser Part Number 757-CUHS20S40H3F
J1: Molex_PicoBlade_53048-0210_1x02_P1.25mm_Horizontal
PV1, PV2: SM940K09L

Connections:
unnamed: D1.2 (A), PV1.1 (+)
unnamed: D1.1 (K), J1.2
unnamed: PV1.2 (-), PV2.1 (+)
unnamed: J1.1, PV2.2 (-)

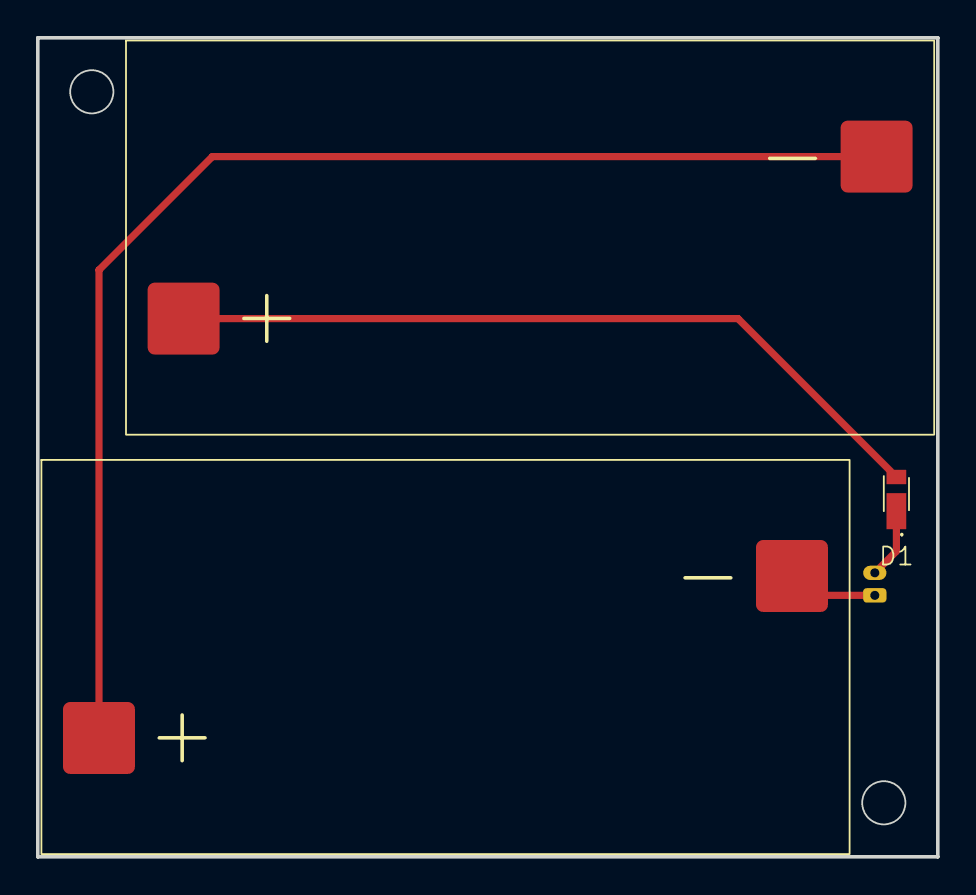
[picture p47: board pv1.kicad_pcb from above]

Board: 2 copper layers, 50.0 x 45.5 mm, 4 parts (1 on the bottom side), 4 nets.
